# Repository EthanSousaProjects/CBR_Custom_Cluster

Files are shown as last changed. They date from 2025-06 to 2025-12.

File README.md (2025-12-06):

# CBR_Custom_Cluster

A custom cluster design for my CBR 125RW6 (2006 carburetor model) to replace the old large mechanical cluster with a smaller simpler design.

The `references` folder contains details on set things on the bike (eg. hole position dimensions, resistance of stock sensor) and thus design requirements, calculations and decisions can be found here.

## License

There are three licenses for this project. All code falls under the AGPLV3 license, all hardware designs fall under the CERN-OHL-S license, all artwork and documentation in the READMEs related to this project are under the CC By-SA license.

This project is based around creating a dash for a honda motorcycle. I have no affiliation with honda or its subsidiaries. This is not an official honda project in anyway.

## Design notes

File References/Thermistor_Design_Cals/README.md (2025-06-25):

# Thermistor Design Calculations

This document details set properties of the stock thermistor of the CBR 125RW6 radiator and the design decisions made because of it. It is supported by charts mathematical equations.

All charts are made in the file: `Design_Charts.ods` it is a Libre Office Calcs document.

## The Active resistance Range of the sensor

From the [Haynes cbr125r manual](https://haynes.com/en-gb/honda-motorcycle/cbr125r/2004-2010) wiring diagram it is clear that the sensor is a thermistor that is wired to ground and the dash sensor. The coolant temperature gauge has 3 wires connected to it: one for Voltage in, One for ground and one wire which goes to the sensor which is also wired to ground. I could not find resistance values of the sensor which match up with the needle positions of the gauge from the manual. Therefore, testing was required to find the resistance values the sensor can achieve and what that would look like on the gauge.

This testing was conducted by powering the gauge with 12 volts through the power pins (Vin and ground) determined from the wiring diagram in the manual. Then connected the sense wire to one end of a resistor/ resistor chain (resistors in parallel) with the other end of the resistor / resistor chain to ground. This simulates the thermistor at a specific resistance which would normally correspond to a certain temperature. The needle position will be noted and the resistance adjusted until we found resistances that matched up with needle positions of interest. Those positions being:

- Just letting off cold side limit

- 25% mark

- 50% mark

- 75% mark

- Just before reaching hot side limit

This relationship was then put into a table and charted to analysis the relationship.

| Needle Position  | Resistance (Ohms) |
| --- | --- |
| 0% **(Note 1)**  | 1000 |
| 25% | 727 |
| 50% | 579 |
| 75% | 470 |
| 100%**(Note 2)** | 377 |

**Note 1:** When the needle just starts to move off edge. Any value above this will not move needle.

**Note 2:** When needle just reaches top edge. Any value lower than this will stay at the top edge.

If we were to chart this data including the effect of higher and lower resistances at the limits we would get:

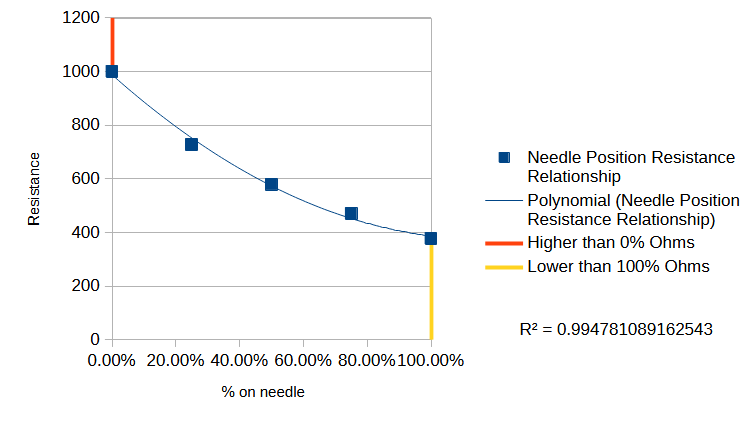
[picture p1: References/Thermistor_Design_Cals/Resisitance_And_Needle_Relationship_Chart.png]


From the results and charts gathered from the test we have determined the active range of the needle gauge on the stock bike and thus the range of interest for the new dash project.

## Nano Sensor Circuit Design

To detect the resistance value we need to use a [voltage divider](https://en.wikipedia.org/wiki/Voltage_divider) circuit. For our use case, our voltage divider circuit will look like:

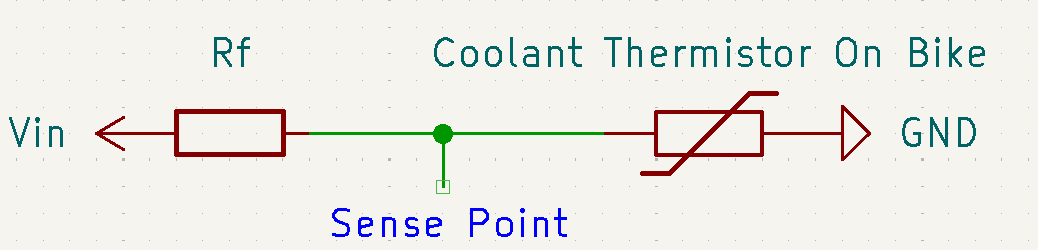
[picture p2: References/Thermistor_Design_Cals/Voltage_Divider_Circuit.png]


From this we can develop an equation to find the voltage at the sense point and as we know the voltage limit on the [Arduino Nano ESP32](https://docs.arduino.cc/hardware/nano-esp32/) is 3.3V set the voltage limit at the sense point.

$Vin { Rx \over Rx + Rf} \le 3.3V$

Where:

- $Rx$ is the resistance of the coolant thermistor on the bike

- $Rf$ is the fixed resistor we have to add

- $Vin$ is the source voltage into the line

If we think about what could happen in the circuit based on the data collected. It is possible in the most extreme cases for the sensor resistance to become practically 0 if the bike were to get too hot. Therefore, if we set $Rx$ to 0 Ohms and complete the calculation we find the $Vin$ must not exceed $3.3V$.

From this, we now know that $Vin$ must be $3.3V$ to get the largest sensing voltage range out of our micro controller.

It is also possible for the sensor to read infinite resistance if the bike were to get too cold. Therefore meaning that we can never reach a voltage sense of 0V as $Rx$ is the numerator of the fraction. We can however, find a $Rf$ value that will give us the most ideal voltage curve that is as linear as possible with a satisfactory voltage range.

To do this we can reconfigure our equation above to:

$3.3 {Rx \over Rx + Rf}=V_{sense}$

We can then use this equation to plot multiple lines of different $Rf$ values to find the most appropriate one.

If we first plot a chart of the voltage differences between the top and bottom values we get a chart like:

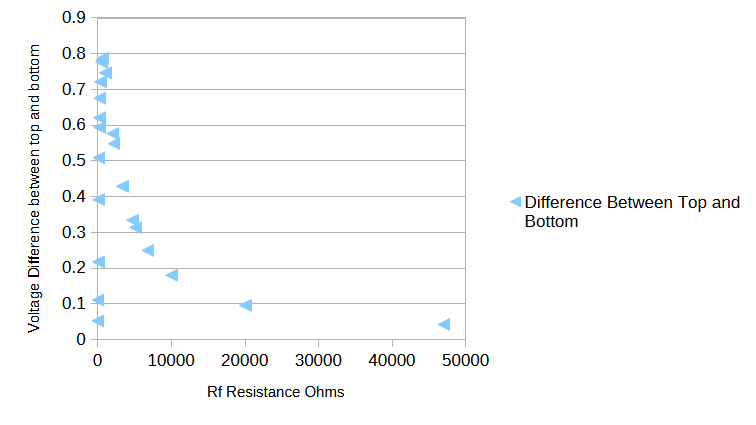
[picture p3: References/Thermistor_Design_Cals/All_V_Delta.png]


This cart shows us that in the best case scenario the voltage range is at best around 0.8V. This is very low but unfortunately we have a very large active range of the sensor so we have to use it. If we remove all the points with a Voltage delta of less than $0.5V$ we get:

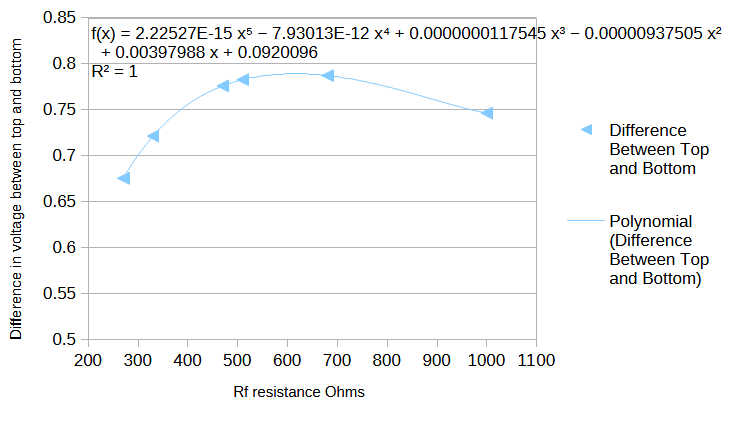
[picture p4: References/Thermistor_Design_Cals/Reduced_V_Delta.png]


We can plot a like onto this and see that we get a polynomial trend for the range of $Rf$ between approximately between 200 and 1100 Ohms.

We get a very good fit with a power of 5 polynomial (R value = 1). It also shows that the most ideal resistor is about 600 Ohms. As that is not a standard resistor I will choose either 510 or 680 Ohms. Either will be fine.

We may also want to have a look at the trend line between our points of interest of the reduced $Rf$ value range. We get a chart like the one bellow:

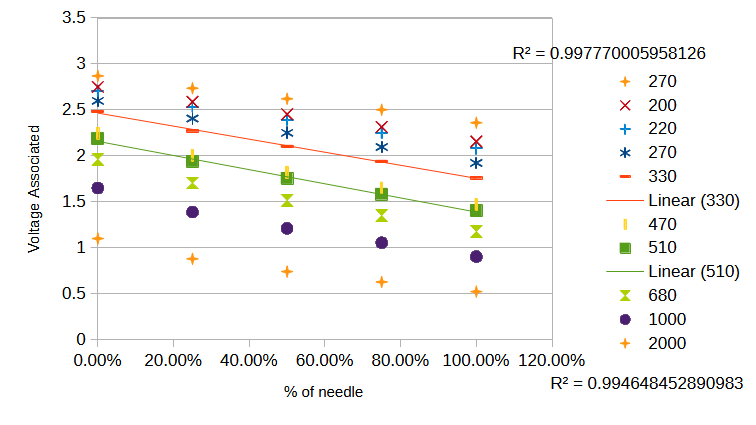
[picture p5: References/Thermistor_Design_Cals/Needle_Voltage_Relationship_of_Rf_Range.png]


We can see from this that between the points of interest we have a very linear relationship with high R values. Therefore, a linear relationship can be established and used in code making things simpler.

Due to the 12 bit resolution of the [Arduino nano esp32](https://docs.arduino.cc/tutorials/nano-esp32/cheat-sheet/) meaning we get values between 0 and 4095 (0V for 0, 3.3V for 4095) we can find the maximum amount of steps in our sensor. With a 510 Ohm resistor we get approximately a delta V of 0.77 volts.

Voltage per step: ${3.3 \over 4095} \approx 0.000806$

Amount of steps in interest range = ${0.77 \over 0.000806} \approx 955$ steps.

This range is satisfactory for my use case.

 From all this, a 510 Ohm resistor for $Rf$ will be used giving use satisfactory resolution.

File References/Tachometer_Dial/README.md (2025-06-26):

# Tachometer Dial Reference

This reference refers to the dimensions of the tachometer dial face which determines many of the PCB size and placement requirements and the mechanical design of the dash project.

The Tachometer face used is from a Honda CBR 600F as the max RPM value is similar to the CBR 125RW6 I have and I like how the dial is even on both sides of the center line instead of it being offset values. I also like it as the speedometer dial face is the same dimensions as the tachometer one allowing me to switch from a tachometer dial to a speedometer dial if I wanted to.

I purchased this dial gauge face from [newtacho.de](https://www.newtacho.de/shop/honda-en/speedometer-dials-gauge-honda-cbf-600/?lang=en) which is a German based company that sells around Europe but other sellers will likely offer the same thing.

The reference dimensions are found by taking a top down image of the dial face with a ruler next to it for scale. This is then imported into [FreeCAD](https://www.freecad.org/), scaled and draw over to get a CAD model of the dial face. Once a CAD model is made it is used to make an engineering drawing which is used as reference for a reference footprint in the Full circuit schematic. This CAD model is also used in the mechancial design as a reference for case dimensions.

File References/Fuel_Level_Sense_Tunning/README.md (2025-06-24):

# Fuel Level Reference Calculations conclusion

To use the stock fuel level sensor we have to understand how the current sensor operates in the bike.

From a [Haynes repair manual for the CBR 125R 2004-2010](https://haynes.com/en-gb/honda-motorcycle/cbr125r/2004-2010) manual for the CBR 125R. it states the following with regards for the resistance between wires of the fuel level sensor that go from the sensor up to the stock cluster:

| Wire Colors | Full Position | Empty Position |
| --- | --- | --- |
| Green - Blue/White | 556 Ohms | 33 Ohms |
| Green - Yellow/White | 33 Ohms | 556 Ohms |
| Blue/White - Yellow/White | 600 Ohms | 600 Ohms |

It must be noted that the Green wire is a ground wire on the bike. Therefore we can make the conclusion that the fuel sensor is a potentiometer where the ground is the whipper position. An image of the circuit can be seen bellow.

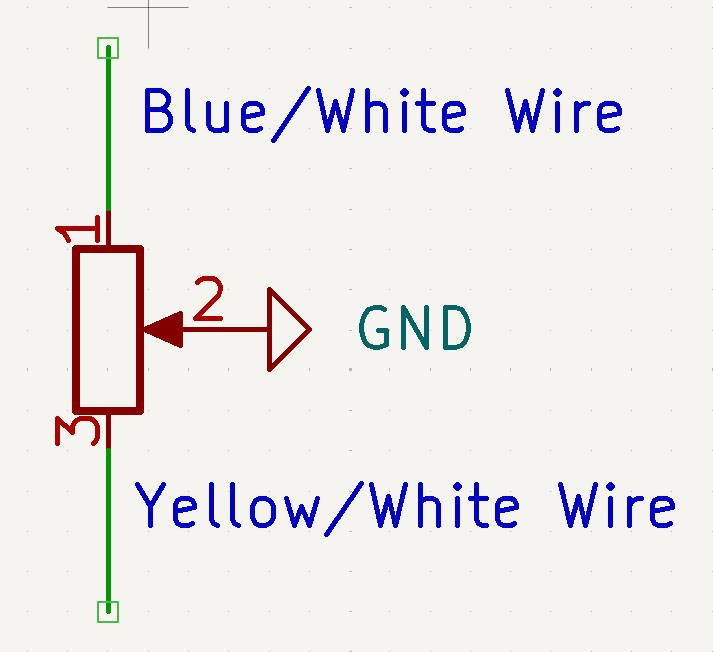
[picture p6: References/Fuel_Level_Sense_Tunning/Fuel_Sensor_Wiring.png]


Now that we know how the sensor is wired, we can create a circuit of how our system needs to be wiring together to measure the resistance of the sensor and thus determine how full the tank is. This will involve a [voltage divider circuit](https://en.wikipedia.org/wiki/Voltage_divider) to get a voltage between a known resistance and a variable one (the variable one being the sensor in this case).

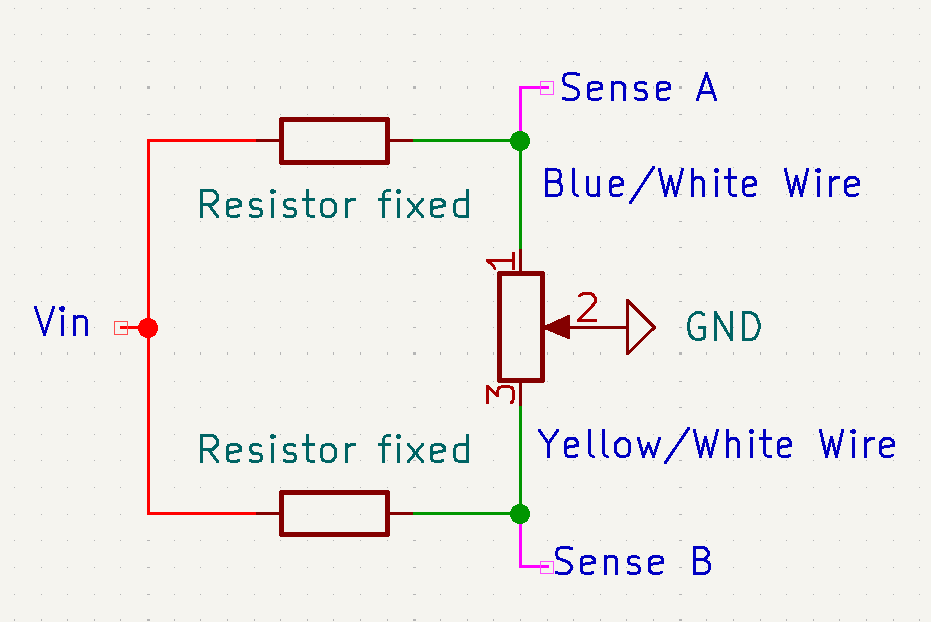
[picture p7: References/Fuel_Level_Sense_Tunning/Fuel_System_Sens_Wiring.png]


Now that we have developed the system wiring, we can develop equations to find the voltage at positions Sense A and Sense B. Please note that these positions will have identical reactions but in opposite directions. Thus we can find the fixed resistance in one leg and thus will know what is required for the other leg. Just note that resistance values correspond to opposite values of fullness.

$Vin{ {Rx} \over {Rt} } \le 3.3$ where $Rt = Rx + Rf$.

- $Vin$ is the driving voltage of the circuit. For my use case i will be using 9V as that is one of my standard voltages of my design.

- $Rx$ is the value of the potentiometer resistance. The values we are mostly interested in are the maximum and minimums which are 566 Ohms and 33 Ohms respectively. This is the driver for what the voltage will be at the sense side.

- $Rt$ is total resistance between the fixed resistor ($Rf$).

- The $3.3$ is the maximum voltage that my micro controller can take which is why it is on the right side of the inequality as for any $Rx$ value i need it to always be bellow $3.3 V$.

If we think about the [Equations behind a voltage divider](https://en.wikipedia.org/wiki/Voltage_divider) we will know that in our case the higher the $Rx$ value the higher the voltage will be. Therefore, we can find the minimum value of $Rf$ required to make sure the sense voltage never exceeds $3.3V$.

$9 {556 \over 556 + Rf} \le 3.3$

${556 \over 556 + Rf} \le {3.3 \over 9}$

$556 \le 0.36667(556 + Rf)$

${556 \over 0.36667} \le 556 + Rf$

$1543.5 - 566 \le Rf$

$977.5 \le Rf$

Therefore, $Rf$ must be greater than $977.5$ Ohms. If we use a standard resistor, the closest value higher than this is a 1 Kilo ohm resistor. This that is what will be used.

All further calculations are included in the file named `Level_VS_Resistance_Test_calcs.ods` which is a Libre Office Calc document.

With all this information, If we assume the relationship is linear between the resistance and fullness of the tank, we can predict how full the tank will be. It must be noted however that the voltage will not be linear. Therefore we will get some offset from the predicted value of fulness if we assume that the voltage is linear between fullness as well. This can be seen in the chart bellow:

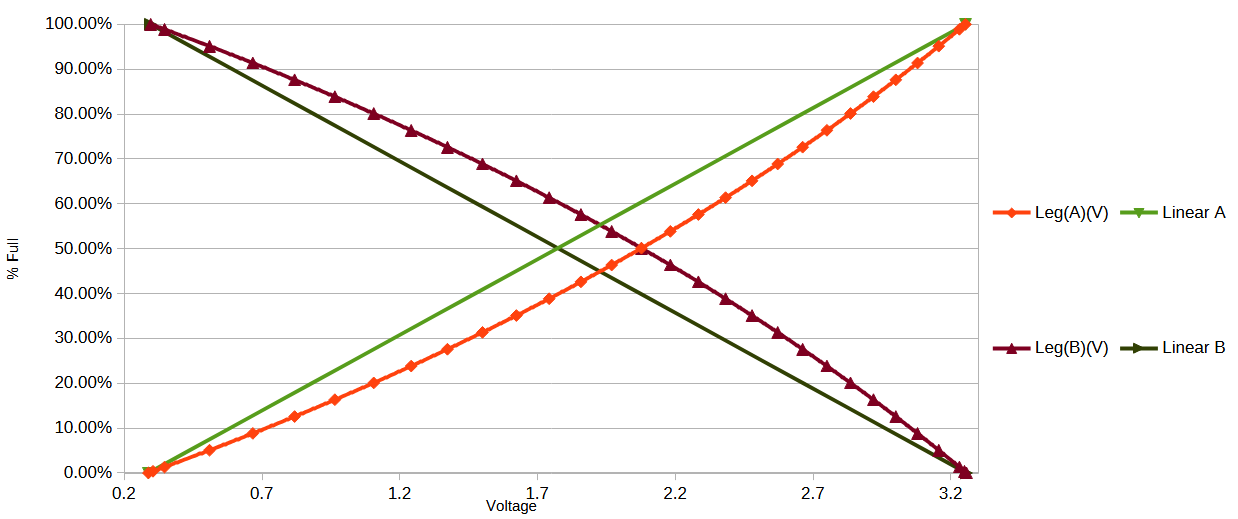
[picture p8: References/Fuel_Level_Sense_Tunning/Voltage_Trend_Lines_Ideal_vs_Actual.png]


To mitigate this we can use the average of the legs predicted values to get a value much closer to the actual value of the tank fullness. This can be seen in the chart bellow:

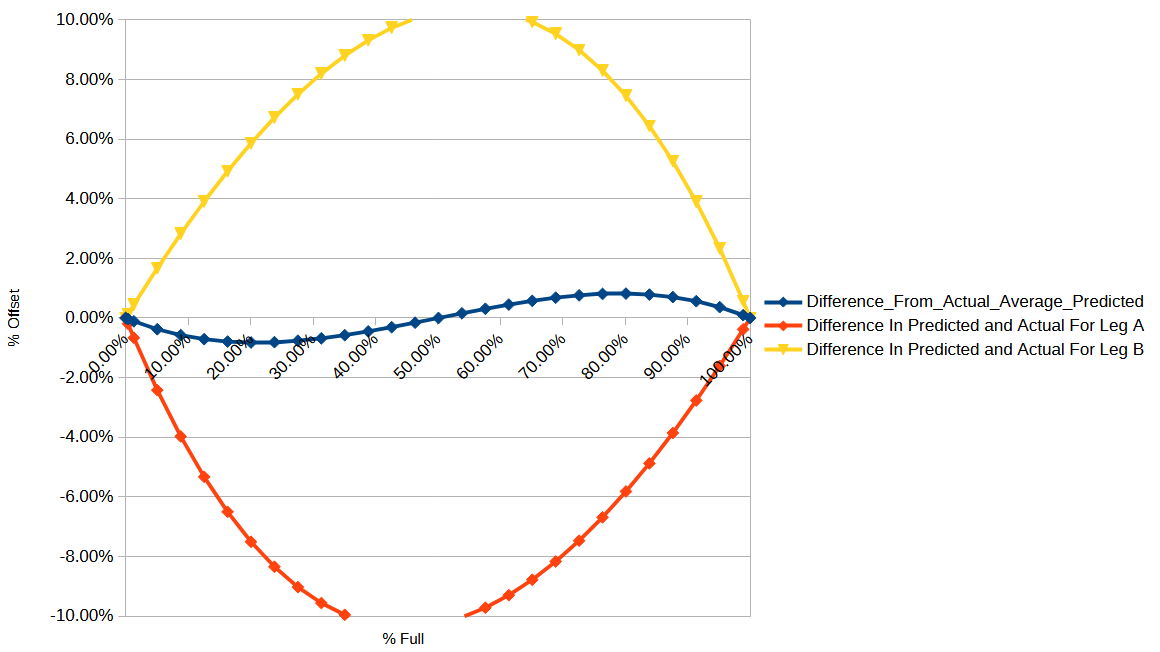
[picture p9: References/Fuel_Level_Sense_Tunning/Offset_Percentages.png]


We are not fully at the actual value but we are much closer compared to the upwards of 10% off if we were to only look at one leg. As very a precise accuracy is not needed the 1ish % offset is fine.

We now know the requires in our schematic for our dash and it can be implemented.

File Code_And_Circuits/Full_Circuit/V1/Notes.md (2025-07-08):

# Notes following the V1 design

- Through testing the following pin config is needed for the stepper to operate correctly `Stepper gauge_stepper(600, 2, 3, 5, 4);`

- Display works as expected using the testing code found in the test script folder. Makes a nice white colour with all the resistors.

- All power lines are working as expected getting all voltage levels i would expect

- Intesting note when powered on all lights sometimes pop on.

## Improvements for V2 design

- Make a smaller diameter.

- Consider a module based setup instead of using the nano for packaging reasons. (ESP32-S3 based) is more advanced and will need to worry about usb port but would help slim down packaging and may make more pins avaliable for usage.

- Consider the use of multiple PCBs

- Adjust capacitors to use standard values i have by putting them in parallel if needed as some values i do not have.

- Reconsider the power supplies, smaller?, Can i power nano with just 3.3V eliminatig need for 9V one, etc.

- Move all the components (caps, resistors, chips, etc) that do not have to be on the top layer to the bottom layer.

- Move all the traces to the bottom layer/ as many as possible.

- Try to implement the logging controller with GPS, SD card, etc

- Reconsider pinouts to work a bit better for the stepper driver to keep all pins on the same layer.

- Consider an SMD mounting for anything that is currently through hole. eg. steppper driver, nano, 

- Change 10 uF caps to electrolitic or decrease to be an SMD version (eg. 0.1 uF) 0.1uF for noise filtering and elecolitic to hold charge for componentes suddenly drawing it. Reconfigure it to work a bit better and ceramic caps do not reach high values.

- Add in underlights for RPM gauge/ speedo gauge that I forgot about. Make through hole 5mm ones or consider using standard W5W lights by putting holes in PCB at certain spots. Or consider using SMD mounting leds for smaller packaging.

- Reconsider mounting hole locations to be more evenly distrabuted.

- Reconsider some footprints that can be a socket instead of component directly soldered on.

- Implement diodes just maybe reconsider smd vs through hole

- re implement caps

- reconsider how display resistors are implemented as if want other colour than white really hard to desolder smd bits could make solder pad which could be good.

- Reconsider how to display speed can it work on the LCD as the alphanumeric takes up a bit too much space in current design. Testing required.

- Change the pins around after the logic level shifter to the stepper driver to keep all traces on the same layer and adjust pin config in code to suit.

## Extra notes on improvements and what to tackel.

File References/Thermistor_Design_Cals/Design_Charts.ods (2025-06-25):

 | Needle position and Resistance Relationship |  |  | Setup values
 | % on needle | Resistance (Ohms) |  | 1200 | 0
* | 0.00% | 1000
 | 25.00% | 727
 | 50.00% | 579
 | 75.00% | 470
** | 100.00% | 377
 | * Note 0 % on needle is when it just starts to move.
 | ** Note 100% on needle is when it just gets there.
 | Different Rf values test
 | Use standard Resistance values instead of custom so that standard resistor can be used Mainly testing with resistor range I personally have
 | % on needle | 0.00% | 25.00% | 50.00% | 75.00% | 100.00%
 | Resistance (Ohms) | 1000 | 727 | 579 | 470 | 377
 | Rf Values to test |  |  |  |  |  | Difference Between Top and Bottom
 | 10 | 3.26732673267327 | 3.25522388059701 | 3.24397283531409 | 3.23125 | 3.21472868217054 | 0.0525980505027248
 | 22 | 3.22896281800391 | 3.20307076101469 | 3.17920133111481 | 3.15243902439024 | 3.11804511278196 | 0.110917705221959
 | 47 | 3.15186246418338 | 3.09961240310078 | 3.05223642172524 | 3 | 2.93419811320755 | 0.217664350975834
 | 100 | 3 | 2.90096735187424 | 2.8139911634757 | 2.72105263157895 | 2.60817610062893 | 0.391823899371069
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

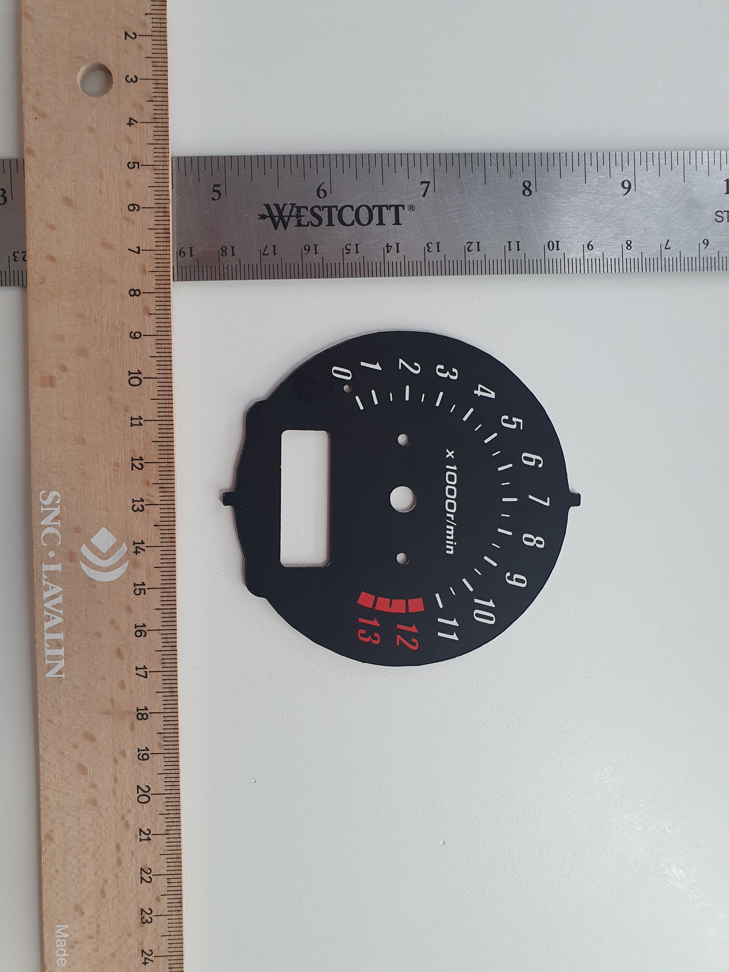
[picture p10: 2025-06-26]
References/Tachometer_Dial/Tach_Face_Reference_Image.jpg

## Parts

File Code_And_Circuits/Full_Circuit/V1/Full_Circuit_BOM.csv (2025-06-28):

Reference | Qty | Value | DNP | Exclude from BOM | Exclude from Board | Footprint | Datasheet
A1 | 1 | Arduino_Nano_ESP32 |  |  |  | Module:Arduino_Nano | https://docs.arduino.cc/resources/datasheets/ABX00083-datasheet.pdf
A3 | 1 | Arduino_Nano_ESP32 | DNP |  | Excluded from board | Module:Arduino_Nano | https://docs.arduino.cc/resources/datasheets/ABX00083-datasheet.pdf
C1,C5 | 2 | 1000PF |  |  |  | Capacitor_SMD:C_0805_2012Metric_Pad1.18x1.45mm_HandSolder | ~
C2,C3,C4 | 3 | 1000PF | DNP |  | Excluded from board | Capacitor_THT:C_Disc_D3.0mm_W2.0mm_P2.50mm | ~
C6,C19 | 2 | 0.1 uF |  |  |  | Capacitor_SMD:C_0805_2012Metric_Pad1.18x1.45mm_HandSolder | ~
C7 | 1 | 0.33uF |  |  |  | Capacitor_SMD:C_0805_2012Metric_Pad1.18x1.45mm_HandSolder | ~
C8,C9,C10,C11,C12,C13,C14,C15 | 8 | 1uF |  |  |  | Capacitor_SMD:C_0805_2012Metric_Pad1.18x1.45mm_HandSolder | ~
C16 | 1 | 100uF | DNP |  | Excluded from board | Capacitor_SMD:C_0805_2012Metric_Pad1.18x1.45mm_HandSolder | ~
C17,C18 | 2 | 10 uF |  |  |  | Capacitor_THT:C_Disc_D3.0mm_W1.6mm_P2.50mm | ~
D1 | 1 | LED_Right_Indicator(Yellow_LTH5MM12VFR4700) |  |  |  | LED_THT:LED_D5.0mm | ~
D2 | 1 | LED_High_Beam(Blue_LTH5MM12VFR4600) |  |  |  | LED_THT:LED_D5.0mm | ~
D3 | 1 | LED_Neutral(Green_LTH5MM12VFR4500) |  |  |  | LED_THT:LED_D5.0mm | ~
D4 | 1 | LED_Left_Indicator(Yellow_LTH5MM12VFR4700) |  |  |  | LED_THT:LED_D5.0mm | ~
D5,D7,D8,D9,D10,D11,D12,D13 | 8 | LED_2.2V_20ma |  |  |  | LED_THT:LED_D5.0mm | ~
D6,D14 | 2 | 1N4007 | DNP |  | Excluded from board | Diode_THT:D_DO-41_SOD81_P10.16mm_Horizontal | http://www.vishay.com/docs/88503/1n4001.pdf
DS1 | 1 | NHD-C12832A1Z-FS_RGB_-FBW-3V |  |  |  | Added_Footprints:NHDC12832A1ZFSRGBFBW3V
H1,H2,H3 | 3 | MountingHole |  | Excluded from BOM |  | MountingHole:MountingHole_3.2mm_M3 | ~
H4 | 1 | MountingHole | DNP | Excluded from BOM | Excluded from board | MountingHole:MountingHole_3.2mm_M3 | ~
J1 | 1 | Micro_SD_Card_Slot | DNP |  | Excluded from board | Connector_Card:microSD_HC_Wuerth_693072010801 | https://www.we-online.com/components/products/datasheet/693072010801.pdf
J2 | 1 | Main_Power_In_JST-XH |  |  |  | Connector_JST:JST_XH_B2B-XH-A_1x02_P2.50mm_Vertical | ~
J3 | 1 | Warning_Lights_JST-XH |  |  |  | Connector_JST:JST_XH_B4B-XH-A_1x04_P2.50mm_Vertical | ~
J4 | 1 | Signals_RPM_Temp_Fuel_JST-XH |  |  |  | Connector_JST:JST_XH_B4B-XH-A_1x04_P2.50mm_Vertical | ~
J5 | 1 | Speed_Pulser_Setup_Signal_JST-XH |  |  |  | Connector_Wire:SolderWirePad_1x01_SMD_1x2mm | ~
J6 | 1 | Alphanumeric_Qwiick_JST-XH |  |  |  | Connector_JST:JST_XH_B4B-XH-A_1x04_P2.50mm_Vertical | ~
JP1 | 1 | Pull up Jumper |  | Excluded from BOM |  | Jumper:SolderJumper-3_P1.3mm_Open_RoundedPad1.0x1.5mm_NumberLabels | ~
JP2 | 1 | address jumper A2 | DNP | Excluded from BOM | Excluded from board | Jumper:SolderJumper-3_P1.3mm_Bridged12_RoundedPad1.0x1.5mm_NumberLabels | ~
JP3 | 1 | address jumper A1 | DNP | Excluded from BOM | Excluded from board | Jumper:SolderJumper-3_P1.3mm_Bridged12_RoundedPad1.0x1.5mm_NumberLabels | ~
JP4 | 1 | address jumper A0 | DNP | Excluded from BOM | Excluded from board | Jumper:SolderJumper-3_P1.3mm_Bridged12_RoundedPad1.0x1.5mm_NumberLabels | ~
JP5 | 1 | Write Protection Jumper | DNP | Excluded from BOM | Excluded from board | Jumper:SolderJumper-2_P1.3mm_Open_RoundedPad1.0x1.5mm | ~
M1 | 1 | GY-GPS6MV2 | DNP |  | Excluded from board | Added_Footprints:GY-GPS6MV2
M2 | 1 | Stepper_Motor_bipolar |  |  |  | Added_Footprints:X27-168 | http://www.infineon.com/dgdl/Application-Note-TLE8110EE_driving_UniPolarStepperMotor_V1.1.pdf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
M3 | 1 | Accelerometer and Gyroscope (BMI160 Module) | DNP |  | Excluded from board | Added_Footprints:BMI160_Module
N1 | 1 | Tachometer Reference |  |  |  | Added_Footprints:Dial_Gauge_Reference_CBF600 | ~
R1,R2,R3,R4 | 4 | 200R |  |  |  | Resistor_SMD:R_0805_2012Metric_Pad1.20x1.40mm_HandSolder | ~
R5,R10 | 2 | 3.3KR |  |  |  | Resistor_SMD:R_0805_2012Metric_Pad1.20x1.40mm_HandSolder | ~
R6,R7,R8,R11 | 4 | 1KR |  |  |  | Resistor_SMD:R_0805_2012Metric_Pad1.20x1.40mm_HandSolder | ~
R9 | 1 | 510R |  |  |  | Resistor_SMD:R_0805_2012Metric_Pad1.20x1.40mm_HandSolder | ~
R12,R13,R14,R15,R16,R17,R18,R19 | 8 | 100R |  |  |  | Resistor_SMD:R_0805_2012Metric_Pad1.20x1.40mm_HandSolder | ~
R20 | 1 | 10KR |  |  |  | Resistor_THT:R_Axial_DIN0204_L3.6mm_D1.6mm_P7.62mm_Horizontal | ~
R22 | 1 | 56R |  |  |  | Resistor_SMD:R_0805_2012Metric_Pad1.20x1.40mm_HandSolder | ~
R23,R24 | 2 | 6.8R |  |  |  | Resistor_SMD:R_0805_2012Metric_Pad1.20x1.40mm_HandSolder | ~
R25,R26 | 2 | 4.7KR |  |  |  | Resistor_SMD:R_0805_2012Metric_Pad1.20x1.40mm_HandSolder | ~
R27,R28,R29,R30 | 4 | 100KR | DNP |  | Excluded from board | Resistor_SMD:R_0805_2012Metric_Pad1.20x1.40mm_HandSolder | ~
SW1 | 1 | SW_Push_JST-XH_Input |  |  |  | Connector_JST:JST_XH_B2B-XH-A_1x02_P2.50mm_Vertical | ~
TP1,TP2,TP3 | 3 | TestPoint |  |  |  | Connector_PinHeader_2.54mm:PinHeader_1x01_P2.54mm_Vertical | ~
TP4,TP5,TP6 | 3 | TestPoint | DNP |  | Excluded from board | Connector_PinHeader_1.00mm:PinHeader_1x01_P1.00mm_Vertical | ~
U1 | 1 | R-78E3.3-0.5 |  |  |  | Converter_DCDC:Converter_DCDC_RECOM_R-78E-0.5_THT | https://www.recom-power.com/pdf/Innoline/R-78Exx-0.5.pdf
U2 | 1 | L293D |  |  |  | Package_DIP:DIP-16_W7.62mm | http://www.ti.com/lit/ds/symlink/l293.pdf
U3 | 1 | TEC2-1219WI |  |  |  | Converter_DCDC:Converter_DCDC_TRACO_TMR-xxxx_THT | https://www.tracopower.com/products/tec2wi.pdf
U4 | 1 | L7805 |  |  |  | Package_TO_SOT_THT:TO-220-3_Horizontal_TabDown | http://www.st.com/content/ccc/resource/technical/document/datasheet/41/4f/b3/b0/12/d4/47/88/CD00000444.pdf/files/CD00000444.pdf/jcr:content/translations/en.CD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
U5 | 1 | TXB0104D |  |  |  | Package_SO:SOIC-14_3.9x8.7mm_P1.27mm | http://www.ti.com/lit/ds/symlink/txb0104.pdf
U6 | 1 | 74HC595 |  |  |  | Package_DIP:DIP-16_W7.62mm_Socket | http://www.ti.com/lit/ds/symlink/sn74hc595.pdf
U7 | 1 | CAT24C128 |  |  |  | Package_SO:SOIC-8_3.9x4.9mm_P1.27mm | https://www.onsemi.com/pub/Collateral/CAT24C128-D.PDF

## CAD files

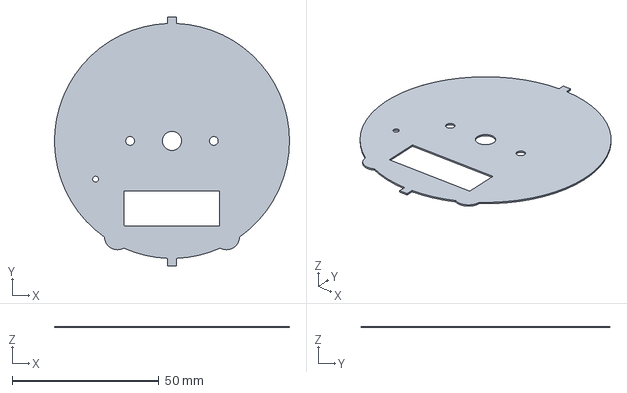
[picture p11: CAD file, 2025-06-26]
References/Tachometer_Dial/Tach_Face_Reference_CAD_Model.FCStd
80.0 x 84.7 x 0.5 mm

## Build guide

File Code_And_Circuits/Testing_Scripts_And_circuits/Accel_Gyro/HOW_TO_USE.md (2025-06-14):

# Accelerometer and Gyroscope module data collection.

This testing script and circuit is used to test the functionlity of the BMI160 6 axis accelerometer and gyroscope. Specifically the I2C interface (there is an SPI interface I am not using). This script is based around using an arduino Nano running the script but, any board with I2C compatability should work. You will just have to change the ini file if you do.

For the BMI160 i purchased it from [Kunkune](https://kunkune.co.uk/shop/arduino-sensors/bmi160-6-axis-motion-tracking-accelerometer-gyroscope-module/) but there are other retailers selling the same module.

There is a schematic and test PCB made in KICAD in the folder `Circuit_Accel_Gyro` of how  everything should be connected together when using the I2C interface.



Once everything is connected make sure the [DFRobot BMI160](https://docs.arduino.cc/libraries/dfrobot_bmi160/) library is installed and avaliable to the project. Compile and upload the code. When you connect the board to the serial terminal you should see the acceleration and gyroscope values appear. These are the raw values from the sensor every secound just so that you are able to read the values a bit easier to read. To get more accurate values for processing you will need to remove the delay of 1000ms to increase your sampling rate.

I have not done any post processing on this script to get things like pitch and roll but i have come accross a few resources on the mathematics behind it if you are interested.

- [ESP32 with BMI160 Accelerometer & Gyroscope Sensor](https://how2electronics.com/esp32-with-bmi160-accelerometer-gyroscope-sensor/)
- [Measure Pitch, Roll, Yaw with MPU6050 + HMC5883L & ESP32](https://how2electronics.com/measure-pitch-roll-yaw-with-mpu6050-hmc5883l-esp32/)
- [Measuring Roll, Pitch, and Yaw Using 3-Axis Gyro on the MPU6050](https://toptechboy.com/measuring-roll-pitch-and-yaw-using-3-axis-gyro-on-the-mpu6050/)
- [Towards understanding IMU: Basics of Accelerometer and Gyroscope Sensors and How to Compute Pitch, Roll and Yaw Angles](https://atadiat.com/en/e-towards-understanding-imu-basics-of-accelerometer-and-gyroscope-sensors/)
- 

Big thanks to the DF robot team on their library and [their tutorial on their module](https://wiki.dfrobot.com/Gravity__BMI160_6-Axis_Inertial_Motion_Sensor_SKU__SEN0250) which was helpful for me getting my module to work.

Big thanks to [hanyazou](https://github.com/hanyazou) on github for his [BMI160 library README.md](https://github.com/hanyazou/BMI160-Arduino) helping me to wire my sensor together.

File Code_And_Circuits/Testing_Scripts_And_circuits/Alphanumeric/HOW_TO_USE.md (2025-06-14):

# Testing the Spark fun alpha Numeric Display

This testing sript and circuit is used to test the functionality of the SparkFun Qwiic Alphanumeric Display in it's ability to display letters and numbers (speed and units kph or mph). This is based around using an Arduino nano running the script but any board with I2C and the [SparkFun Qwiic Alphanumeric Display Arduino Library](https://docs.arduino.cc/libraries/sparkfun-qwiic-alphanumeric-display-arduino-library/) compatability should work. You will just have to change the ini file if you do.

For this display i purchased it from [Pihut](https://thepihut.com/products/sparkfun-qwiic-alphanumeric-display-purple). I specifically purchased the purple one due to my bikes purple theme. There are other colours. Other colours are avaliable like red, green, blue, white, etc. to fit your wants. You will need to get a qwiic breakout if you do not have a qwiic plug on your device like me. You could also solder header pins to the board following the [hookup guide from sparkfun](https://learn.sparkfun.com/tutorials/sparkfun-qwiic-alphanumeric-display-hookup-guide/all) but i would recommend getting the adaptor cable.

There is a schematic and test PCB made in KICAD in the folder `Circuit_Alphanumeric` of how everything should be connected together. You will require a breakout cable in my design.



Once everything is connected make sure the [SparkFun Qwiic Alphanumeric Display Arduino Library](https://docs.arduino.cc/libraries/sparkfun-qwiic-alphanumeric-display-arduino-library/) is installed and avaliable to the project. Compile and upload the code. You should see all the segments light up. Then you should see a small k is added to the last digit and the display counts up by 1 to 100. Finally, it repeats the counting to 100 but changes the last digit to a small m.

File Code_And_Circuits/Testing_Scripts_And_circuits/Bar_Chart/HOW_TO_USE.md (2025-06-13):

# Bar chart controlled by arduino with shift registers

This testing script and circuit is to the test the functionallity running a LED bar chart off an arduino using a 74HC595 shift register. This allows us to use more LEDs while not taking up too many of our arduino pins. This script is based around an arduino nano but any micro controller should work if you change the board in platform IO.

The 74HC595 shift register gives us the ability to drive 8 LEDs while only using 3 digital pins. This allows us to drive more LEDs than the arduino may normally be able to. I have two which i have purchased from [Kunkune](https://kunkune.co.uk/shop/compatible-with-arduino-compatible-starter-kits/advanced-arduino-r3-compatible-starter-kit/) as part of an arduino kit and [Pihut](https://thepihut.com/products/74hc595-shift-register-3-pack). There are methods to drive multiple of these shift registers in series in eachother. See [this arduino tutorial from Carlyn Maw & Tom Igoe](https://docs.arduino.cc/tutorials/communication/guide-to-shift-out/).

There is a scematic and test PCB made in KICAD in the folder `Circuit_Bar` of how everything should be connected together. You can change around the digital pins just remember to change it in the script as well.



Once everything is connected, compile and upload the code. You should slowly see all the lights light up in sequence before resetting. Some of the sequence is faster than other points due to how the incrementing loop works.

Some complexity of the code you may not understand imeditatly is the [byte](https://docs.arduino.cc/language-reference/en/variables/data-types/byte/) data type and the `<<` operation. The `<<` is a [bit shift left operation](https://docs.arduino.cc/language-reference/en/structure/bitwise-operators/bitshiftLeft/) to help me get the bits in the bytes setup correctly to light up the 0 to x lights. I am basically getting an integer from that operation subrating 1 and then converting back to a byte. [Conversion from Binary to decimal explaination can be found here](https://www.tutorialspoint.com/how-to-convert-binary-to-decimal).

Big thanks to [Elego](https://www.elegoo.com) for their [Arduino tutorials](https://www.elegoo.com/en-gb/pages/download) which got me started with this.

Big thanks to [Jason Clark](https://arduino.stackexchange.com/users/28183/jason-clark) on arduino Stack Exchange for his help on getting a [better way to calculate 2^X instead of using the arduino `pow()` function](https://arduino.stackexchange.com/questions/31191/is-there-a-non-float-alternative-to-pow).

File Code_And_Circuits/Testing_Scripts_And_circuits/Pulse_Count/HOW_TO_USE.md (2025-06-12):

# Pulse Counter for Speed and RPM measurments

This testing script and circuit is used to test a pulse reading/ measuring script. This can then be used to translate the electrical pulses from the speed sensor and/or RPM pulses into speed or RPM data to be displayed on the dash. It is based on using an arduino nano running the RPM_TO_PWM script that is part of the `Testing_Scripts_And_Circuits` folder of this project and using a DOIT ESP32 devkit V1 to figure out the rpm/ count the pulses coming from the nano. Both scripts should work on any other microcontroller using the arduino framework.

It can be noted that we can find the rpm value by finding the time period of a pulse. We can then convert that to a frequency of pulses (... Hz). Once we have the frequency multiplying it by 60 would five the RPM value if you get one pulse per revolution. Slight math adjustment would be needed if you get something different to 1 pulse per rotation.
Speed is a tad more complicated but we can use the same theory of measuring the time of a pulse. If using something like a set of magnets, equally spaced on a wheel with a hall effect sensor picking them up. The time period would be the angle traveled between the two magnets. If we know the diameter or circumfrance, we could find the distance traveled along the circumfrance of the wheel. Therefore we would have distance and time and thus, speed = distance/ time.

It is important to note that the arduino works on 5V and the DOIT esp32 works on 3.3 volts thus a voltage divider was required for my use case. If alternative boards are used please make sure the voltage pulse measured is close to/ is the working voltage of micro controllers. Sending a 5V pulse to a 3.3V device may break the 3.3V device and sending a 3.3V pulse to a 5V device may just not recognise the signal as high.

There is a scematic and test PCB made in KICAD in the folder `Circuit_GPS` of how everything should be connected together. If you are not using the same boards as me, please adjust the voltage divider (resistors) to something more appropriate. Please also connect the grounds of the micro controllers together so that there is a common ground reference point/ plane.

Please note that the Kicad scematic uses a arduino nano ESP32 board instead of the DOit board. The connections are very similar just make sure the pin definitions are correct. I was unable to find a footprint for the DOIT dev kit. The important bit is the circuit divider taking the 5V pulse down to 3.3V if it is required. If it is not then you do not need to have it.



Once everything is connected, start both boards up having a serial monitor attached to each. On the nano you will have to type a RPM value to start the pulsing and on the measurment side you should see RPM and speed values. Verify they are as you expect by making some hand calculations based on your input parameters.

Big thanks to [TinkeringEngineer](https://www.instructables.com/member/TinkeringEngineer/) on instructables with his [Use Arduino to Display Engine RPM project](https://www.instructables.com/Use-Arduino-to-Display-Engine-RPM/) which helped me here improve on my initial idea for calculated speed and rpm.

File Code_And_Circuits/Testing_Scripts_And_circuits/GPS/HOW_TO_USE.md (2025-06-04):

# Recieving GPS data test for CBR dash project

This testing script and circuit is to the test the functionallity of recieving GPS based data to eventually  be used in the dash project for ride logging where i could track a ride. Originally i thought i would use it for a speed value but due to reliabilty issues i have decieded against it. The Script is based around an arduino nano but any micro controller should work if you change the board in platform IO.

Most GPS modules you can buy online work pretty much the same and the most important pins are the power in (VCC/ VIN and GND) and the RX and TX pins. Most other pins are only there for advanced/ more complicated uses. Therefore, all my diagrams / discussions will only discuss those 4 pins. I have purchased a NEO-6M GPS module from [Kunkune](https://kunkune.co.uk/shop/communication-boards/gy-neo6mv2-gps-module-super-signal-with-antenna/). If you are to get a different GPS module, everything here should work. I would recommend getting a module with an external antenna to help with signal reliability. This module has a baud rate of 9600 so will use that for my serial interface. If you have a different baud rate of your module use that specified baud rate.

There is a scematic and test PCB made in KICAD in the folder `Circuit_GPS` of how everything should be connected together. Please note that the rx and tx lines connect to digital pins so that we can use the [software serial](https://docs.arduino.cc/learn/built-in-libraries/software-serial/) library as if we used the built in rx and tx lines we would loss USB serial communication to see things on the board. Please also note that the rx pin lines up with the software tx pin and vis versa for the tx pin. Reversing this will orientation will make the module not work.



Once everything is connected, make sure that the [TinyGPSPlus](https://docs.arduino.cc/libraries/tinygpsplus/) external libarary is installed for the project to parse the [GPS NEMA string](https://aprs.gids.nl/nmea/#vtg). compile and upload the code. If the USB serial interface you should see the current satalites attached, the longitude and latitiude and the speed of the module. If you are inside you may struggle to connect to any satalites thus being outside in an open area in prefered. Once you get a fix the values should all change to a different value than 0.

Big thanks to the developers behind the [software serial](https://docs.arduino.cc/learn/built-in-libraries/software-serial/) library for arduino and the [TinyGPSPlus](https://docs.arduino.cc/libraries/tinygpsplus/) library.

Big thanks to [random nerd tutorials](https://randomnerdtutorials.com/) for there article on the [NEO-6M GPS Module](https://randomnerdtutorials.com/guide-to-neo-6m-gps-module-with-arduino/) helping me with the coding of the module.

Big thanks to [last minute engineers](https://lastminuteengineers.com/) for there in depth article on the [NEO-6M GPS Module](https://lastminuteengineers.com/neo6m-gps-arduino-tutorial/) where i learned alot about the specifics of the module itself.

Lastly big thanks to the [Core electronics youtube creator](https://www.youtube.com/@Core-Electronics) and there video on [adding GPS to a raspberry pi pico](https://www.youtube.com/watch?v=CLsXnSOIYMg) where i learned alot about the inner workings of GPS.

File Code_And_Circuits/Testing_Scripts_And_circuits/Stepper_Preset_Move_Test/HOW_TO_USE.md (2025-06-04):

# Stepper Preset Move Test for CBR Dash Project

This testing script is used to test the wiring and usability of the X27.168 automotive gauge stepper motor with a L293D dual H bridge motor driver. The script attempts to move the stepper a set distance clockwise/ anticlockwise, then the same distance in the oposite rotation. Then half way in the original direction. Then make a half rotation in the oposite direction again.

The stepper motor is from [adafruit](https://www.adafruit.com/product/2424#technical-details) but i purchased the stepper from a reseller in the UK called [pihut](https://thepihut.com/products/automotive-gauge-stepper-motor). The L293D is fairly generic and can be found on most electronics sellers. I purchased this [driver from pihut](https://thepihut.com/products/dual-h-bridge-motor-driver-for-dc-or-steppers-600ma-l293d).

According to the [technical details](https://www.adafruit.com/product/2424#technical-details) provided by adafruit this stepper motor has a maximum step count of 600 steps which is approximatly 315 degrees so each step is approximatly half a degree. Therefore, to test the stepper system, the script will move 600 steps, then -600, then 300 then -300.
During this movement, you should see the needle rotate approximatly 315 degrees, then -315 degrees, 157 degrees then finally -157 degrees. This will help determin if the circuit is setup correctly and if the rpm set is at an appropriate value.

A wiring scematic and testing PCB has been included in the `Circuit_Stepper` folder for your reference. You can change which pins are used as mine was based on how I had everything layed out on a breadboard.



Once everything is connected, make sure the external stepper library has been added to the platformIO project, compile, upload and run the script. If everything is connected correctly, you should see the stepper move. You may have to adjust your stepper speed to make sure it does not skip. After testing i found 20 rpm to be the maximum thus will run mine at 19 rpm.

Thank you to [Joshua Hrisko](https://makersportal.com/blog?author=59b036fc6073554c1cfffef7) for his [write up](https://makersportal.com/blog/2018/1/29/driving-any-stepper-motor-for-less-than-1-with-the-l293) on how to do this and the developers behind the [arduino stepper library](https://docs.arduino.cc/libraries/stepper/#Usage/Examples).

Big thanks to [Wiktor Burdecki](https://github.com/wiciu15) and his github project named [motoHUDsch](https://github.com/wiciu15/motoHUDsch/tree/master) where he made a [KICAD footprint of the 27.168 stepper motor](https://github.com/wiciu15/motoHUDsch/blob/master/motoHUD.pretty/X27-168.kicad_mod) which i have taken as a base to build off and slightly modified it to fit the datasheet for the stepper motor i found [here](https://4tronix.co.uk/zeropoint/x27_spec.pdf) and the one [adafruit](https://cdn-shop.adafruit.com/product-files/2424/2424.pdf) provided.

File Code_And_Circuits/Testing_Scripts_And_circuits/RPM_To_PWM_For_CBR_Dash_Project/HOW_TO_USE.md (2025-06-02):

# RPM to PWM For CBR Dash Project

This testing script is used to produce a signal matching that of the RPM pulse that comes from the CBR when it is turned on. It is designed to run on an arduino nano but by changing the board target, the script should work on other boards.

Made in VS code Platform IO extension (see main README.md for usage information).

The signal gets outputted on pin 13 (D13)(Make sure to connect grounds). A schematic and kicad PCB can be found in the folder `Circuit_RPM_TO_PWM`.

To get this to work, compile and upload code to the nano/ board and connect a serial monitor as the signal does not start without it. The serial monitor tells you how to select an RPM value and when the signal is running and at what simulated RPM is. Use a keyboard only typing in numbers where relevenent and only charters when relevent.

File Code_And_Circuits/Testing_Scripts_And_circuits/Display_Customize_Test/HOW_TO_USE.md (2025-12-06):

# Customizing display testing for CBR dash project

This testing script has been created to test the functionality of using the [U8g2 graphics library for monochrome displays](https://github.com/olikraus/u8g2) on the [NHD-C12832A1Z-FS(RGB)-FBW-3V](https://newhavendisplay.com/128x32-graphic-cog-lcd-fstn-display-with-rgb-backlight/) Newhaven display that will be used for the dash.

This script will include rendering of speed, trip and odometer data. This will cycle through a few numbers to see what it looks like. It will also cycle through different layouts and fonts to see all of them to choose the best one for the dash.

The circuit is the V1 version of the PCB. You could directly wire it instead of using the PCB but for testing to make sure the PCB was correct i used this.

An important note is that I am using the hardware SPI to run my display. That will effect the setup code. The controller on this display is the ST7565R SPI controller this also has an effect on the code if you are using something different. See code comments for better info on setting up the display correctly.

## Unique non ideal wiring and Pin Assignment

An important note on my setup is that I have used one of the hardware SPI pins as the dc pin also known as the A0 pin or register select pin in my use case. I have specifically used the Controller In Peripheral Out (CIPO) (also known as the Master In Slave Out (MISO)) pin as the dc /register select/ A0 pin. This causes some issues as the pin does not get correctly setup when initializing the display class using hardware SPI. To fix this I added in the following code before and after the `u8g2.begin();` line to fix it:

```c++
  pinMode(12,OUTPUT);
  digitalWrite(12,LOW);
```

Ideally you would avoid using any of the hardware SPI pins that are not necessary. However for my use case I was running out of available pins to utilize for the dash so used it.

## Custom Graphics (GIMP method)

I have made some custom graphics that I have used in the testing scripts. This was so that I could load them onto the display to see what it would look like. Some of these graphics will also be used on the final design.

To create all the graphics I used [gimp](https://www.gimp.org/) the file of which is saved in the `Custom_Images` folder.

To setup gimp for this display follow the guide bellow. Note that adjustments can be mode if using a different sized display in the appropriate places (eg 128 by 64 instead of 128 by 32):

1. Create a new file through `File > New`. Setting the image size to your specific display in Pixels(px). For my display it is 128 width, 32 height.

2. For new files the default colour setting is RGB. to set the black and white setting of the lcd graphics display enter `Image > Mode > Indexed`. In this menu select the `Use black and white (1-bit pallet)`. This will set your workspace to be only black and white.

3. If your grid has not appeared. It could be beneficial to you to see it by ticking the toggle in `View` called `Show grid`.

4. Use the pencil tool with the colour set to black and the size set to 1 to start making graphics.

5. Now you are able to draw any graphic you like. To allow for multiple graphics i used layers instead of creating many different files. When exporting I just selected the layers I wanted to see when exported. To add a layer go into `Layer > New Layer...`. In the menu make sure to set the layer to transparent. Now just make the relevant layers visible when you want to export the images.

6. You can import images into gimp to convert them to the bitmap type by dragging the image file into gimp. This can allow you to use images that have been created already which contain more detail but contain the overall shape you want to create in a graphic lcd form. I am not responsible for any copy write or trade mark infringement that may come from you doing this. Any images uploaded to this repo have been made by myself.

    - You may have to resize the image to fit on the display. To do this, select the layer the image is on and go into `layer > Scale layer...`. In the menu select the interpolation method of your choosing (I typically just use none but you can experiment with the different types) adn adjust the image pixel size that works for your use case.
    - Sometimes you may also have to reset the colour mode as importing images may add greyscale elements. The best way to handle this is to set the mode to greyscale or colour instead of indexed then index it again like in step 2. I have found that this normally fixes my issues.

7. Now that the images have been created. We are ready to export it to a C++ file we can load into the arduino nano esp32.

    - Activate the layers you want to export.
    - To export correctly go into `file > Export AS...`
    - In the menu that appears choose the file type of `X BitMap Image` with the file extension of xmb.
    - Make sure to uncheck the X10 format bitmap option if it is checked.
    - Make sure you remember what folder you export to.
    - The image is now exported correctly.

8. In the bitmap image file created in step 7 we can open the file in any text editor/ IDE. In it you will see some define terms at the top of your display size described with a charter array like declaration bellow it starting with `static unsigned char` etc. This is what needs to be copied into our script to be loaded.

9. In the script use the `u8g2.drawXBM(<int y position start>,<int x position start>,<int Display width in pixels>,<int Display height in pixels>,high30seg);` class function to display it to the screen.

Something extra you can do is to load all the images into a header file like I have with this script to decrease the clutter in the main script file. Just make sure you import the header file with the command `#import "<file name>.h"` the the start of the main script.

## What was learnt/ Liked

Through the use of this test script on the display the following conclusions on the different graphics have been made.

- Overall the display was readable in the dash and it would not be necessary to get a larger display for the dash. However, if you struggle to see I would recommend getting a larger dash like the [NHD-C12864DA-FSRGB-FBW-3V3](https://newhavendisplay.com/128x64-graphic-cog-lcd-fstn-wide-view-with-rgb-backlight-and-pins/) from [NewHaven Displays](https://newhavendisplay.com/) for readability reasons. It can be slightly difficult at times to read the display perfectly.
- If you are overlaying multiple bitmap images over each other, you must set the bitmap mode to 1 (transparent = true). This is done via the `.setBitmapMode(<1 for transparent, 0 for opaque>);` function of the display object more information can be found on the [u8g2 coding reference wiki page](https://github.com/olikraus/u8g2/wiki/u8g2reference#setbitmapmode).
- Making and loading bitmap images worked very well. Using them to make static non updating components like RPM, fuel and coolant graphics to then overlay data on top like speed is a good practice. I will use some of the graphics in my private library as a startup sequence graphic when the bike first turns on. I cannot upload them to github due to copyright unfortunately. I would recommend using this to help make static graphics.
- When testing the [Tom Thumb](https://robey.lag.net/2010/01/23/tiny-monospace-font.html) (u8g2_font_tom_thumb_4x6_mn) font, it was found to be too small and nearly unreadable even when resting on a desk. Therefore, reading it on a moving/vibrating motorcycle was going to be next to impossible. Although the font was very small it could still be used for things like odometer data when it needs to be squeezed onto the screen like the tachometer display as any other font was a bit too big. Ideally this font will not be used.
- An alternative to the tiny font that was much more readable while still being compact was the [u8g2_font_5x7_mr](https://github.com/olikraus/u8g2/wiki/fntgrpx11#5x7) font. This font will be the preferred one for any very small text and numbers like odometer and trip data.
- Through testing I found non bold fonts looked better for my use case in my opinion. The 30 high segment test shows this the best. I believe the non bold version of the font looks better in that test over the bold version of the font test. Therefore, non bold fonts will be used in the final dash.
- I think that the 30 pixel high digit segments worked ok but, by not utilizing the full height of the screen, it made it not work as well as the 32 pixel high  digit segment. I also really liked the appearance of the segment. Therefore, it will be used in the final solution in some way.
- I liked the [u8g2_font_t0_30_mr](https://github.com/olikraus/u8g2/wiki/fntgrpttyp0#t0_30) font for displaying the kph value so I will be using it in the final solution.
- I did not like the [u8g2_font_VCR_OSD_mr](https://github.com/olikraus/u8g2/wiki/fntgrpdafont#vcr_osd) font. It looked off to me for this use case. Therefore, it will not be used.
- The spacing of the kph lettering and Odometer data was perfect in the font based speed representation test for me. This spacing will be used to represent speed data on the final solution.
- In the font based speed representation test I liked the [u8g2_font_inr33_mn](https://github.com/olikraus/u8g2/wiki/fntgrpinconsolata#inr33) font to represent speed data. This font will be one of the solutions to display speed data in the final solution.
- For the RPM tests I liked the same RPM version (version a/1). The only disadvantage was the font size used for odometer data. This will be available in the final solution with a different odometer font being utilized. This version will be much simpler to code up as well compared to the ramping one as a bonus.
- Although Coolant and Fuel data is supposed to be represented by the lights on the dash, I liked the ramping coolant and fuel bars representation. The large gap in the middle was not ideal. The ramping fuel and coolant representation will be used in the final solution with some data being added between it to fill the large gap.

## Final decision on what will be used

For the final dash, there will be a number of display options available for use. This will display the different properties (Speed, RPM, Fuel, etc) on different screens. You will toggle between the screens using the buttons that are part of the dash. The final screen options that will appear in the final dash are as follows. The order is the order of which you can toggle through them. The last display option will be kept even after a power cycle so that you dod not need to toggle through all the options to get back to the one you wanted.

1) Settings panel - contains just text saying `Settings` centred on the screen. You will be able to select this page to enter the settings panel to adjust dash properties for calibration. This will use the [u8g2_font_5x7_mr](https://github.com/olikraus/u8g2/wiki/fntgrpx11#5x7) font to describe the settings available when you toggle through each page and the calibration instructions where appropriate. This font is used here as it will be used for other aspects of the dash. Reducing the amount of fonts used on the dash will reduce the storage requirement of the program allowing it to more likely fit onto the microcontroller.
2) Font based Speed Representation - This will be identical to the `font based speed representation` test. The speed numbers will be represented by the `u8g2_font_inr33_mn` font with the starting coordinates of X = 0 and Y = 32. The speed unit (kph or mph) will be represented by the `u8g2_font_t0_30_mr` font with the starting coordinates of X = 80 adn Y = 20. The trip/ odometer data will be represented by the `u8g2_font_5x7_mr` font with the starting coordinates X = 79 and Y = 32. There will be a toggle to cycle through the Odometer, Trip A and Trip B values using the dash buttons.
3) 32 High Segment based speed representation - This will use the 32 high segments in the `32 segment size test with trip and odometer` test. It will have a starting coordinate of X = 0 and Y = 32. The other data like speed unit (kph, mph) and trip/ odometer data will be identical to the setup in the font based speed version described in point 2 above.
4) Same RPM Representation - This will be nearly identical to the `RPM version a/1 test (Same)` version tested. It will use a bitmap to represent the RPM values at the top. The rpm bar will be represented/ generated using the [draw box](https://github.com/olikraus/u8g2/wiki/u8g2reference#drawbox) display class method. The odometer and trip data will be represented using the `u8g2_font_5x7_mr` font with the starting coordinates X = 0 and Y = 32.
5) Fuel and coolant ramping representation - This will be nearly identical to the `Coolant and fuel version a/1 test (Ramping)` version. It will use a bitmap to represent the coolant and fuel logos and will use the [draw box](https://github.com/olikraus/u8g2/wiki/u8g2reference#drawbox) display class method to represent each bar. The main additional aspect that was not included for the test will be the odometer and trip data all being displayed leftward between the coolant and fuel parts of the display but past the bar portions of both. The Odometer value will be at the bottom with trip B above it and trip A at the top all evenly spaced vertically using the `u8g2_font_5x7_mr` font.
T
Finally, separate to the main displays used in the dash. If there is enough storage on the microcontroller, I will add a startup graphics from my private library for fun. If there is not enough program storage I will not include the start up graphic.

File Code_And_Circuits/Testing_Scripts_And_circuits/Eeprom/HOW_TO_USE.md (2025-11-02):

# Eeprom Test for CBR dash project

This testing script is used to test the functionality of the external eeprom chip. The [CAT24C128](https://www.mouser.co.uk/ProductDetail/onsemi/CAT24C128WI-GT3?qs=rZgeL6XvLwaw%2FcBtNmrs8w%3D%3D) eeprom chip is used due to it being an I2C based eeprom chip and the similarity to the 512 Kbit version that is part of the [Sparkfun eeprom break out](https://www.sparkfun.com/sparkfun-qwiic-eeprom-breakout-512kbit.html). This gives a good code reference due to the [library and guide written](https://learn.sparkfun.com/tutorials/qwiic-eeprom-hookup-guide/all) for it. DFrobot have a similar [guide](https://wiki.dfrobot.com/Gravity__I2C_EEPROM_Data_Storage_Module_SKU__DFR0117#Connection%20Diagram) for their eeprom module which uses the same CAT24 eeprom chips that spark fun used. Both guides have been used as reference to create this test script and by effect the full dash code.

The test circuit is the V1 full PCB version with all components included due to the eeprom chip being SMD mounted.

Make sure to include the [sparkfun external eeprom I2C library](https://github.com/sparkfun/SparkFun_External_EEPROM_Arduino_Library/tree/main) in your project.

The script does a few things based on the serial input given to it to test the read and write functionality of the device. In the serial monitor the user is presented with a few options that do different things:

- 1 = Write an integer a user inputs to the first memory address.

- 2 = Read the integer in the first memory address

- 3 = Write a list of numbers into the eeprom starting with the 2nd aviable memory address.

- 4 = Read and find the highest number in the eeprom starting from the 2nd avaliable memory address.

Please note that memory address is dependant on the data types that come before it. For example an int takes 4 bytes (with an esp32 32 bit, 2 bytes with 16bit arduinos) while a float takes 4. Therefore, for an int in the first memory address the next avalaible memory address would be the 5th one (remember indexing starts at 0 thus memory index is 4 for 5th position).

## Why these features are tested

The features above are tested so that we are able to have precistant constantly undating data with the dash. Options 1 and 2 in the testing script is for testing the feasability of saving calibration data to the eeprom chip. Options 3 and 4 are for testing the ability to save odometer data into the eeprom. See the bellow note on odometer data problems.

## Important note on Odometer and trip meter data

Unlike most data that would be saved to this eeprom. Odometer and trip data constantly need to be updated very frequently. One concern is wear of the memory addresses if only one is used for each. Each address has a finite ammount of times it can be written to, thus constatly writting to one will make it fail very quickly. This can be mitigated by using a wear leveling stategy. Implementing this will help the eeprom chip to last longer.

For trip data, the last trip reset value n(when you reset the trip distance) will be retained in the eeprom. This means that the actual value will have to be calculated by comparing it to the current odometer reading. At the initial startup, the eeprom trip reset value will be read and compared against the odometer reading to give the trip value. This will be saved and updated in ram by the same ammount that the odometer reading is updated with. This allows less writes to the eeprom chip saving write lifes.

Odometer data is where wear leveling is nessary as the value must be imediatly saved to eeprom incase the bike suddenly shuts down thus, wear leveling is needed. The way this will work is by iterating over each memory address till the end of the addresses is reached. Once the last memory address is reached, it will return to the first address to continue the same process. This means that the writes are spread over many memory addresses leveling out the wear due to odometer readings. At startup, the memory addresses for the odometer data will be read. The highest value and it's position will be loaded into RAM so that the dash has accurate odometer readings and knows the last location it wrote to. For each increase of 0.1Km the odometer reading will be captured in eeprom. The start memory address for this is dependent on how much memory is required for calibration data for the dash. Similarly the end memory address is dependent on the size of the data type that needs to be written and the size of the eeprom chip. For example, we can write to memory addresses 0 to 9 where each address is a byte (8 bits,10 bytes worth of memory). Assume there is no static data and it is just odometer data. Asssume we are using floats to hold odometer data (4 bytes). We can start at memory address 0 then write to address 4 (first value sits in addresses 0-3, secound in 4-7). Even though we have addresses 8 and 9. We are unable to write to them as we need two more bytes to write the full float value.

Odometer data will be an integer to avoid errors with floating point math. For esp32s they work on 32bit microprocessors meaning that ints are 32 bits instead of the typical 16 bits in arduino. This means that the max int value is 2,147,483,647. This is plenty high enough for an odometer reading if using my ideal unit of Km. The dash will use all SI units for data and convert when displaying data. It must be noted that the first value of the int will represent the 0.1 of a kilometer (100 meters). Everytime the odometer reading updates by that 0.1Km it will be saved to eeprom to reduce writes. At run time, a separate variable will keep track of how much distance has been traveled and once it reaches the 0.1km threshold it will trigger an odomeeer reading update. It will then reset it's self back to 0 to get back to that 0.1km threashold. The exact unit it will use is still to be decided as of writting (could be cm to stick to int math or it could be m to use floating point math). This will clearly lead to the odometer reading being a bit lower than the actual distance traveled but for my use case that is ok. It will also negate any addition problems with floating point math if it is used.

This test script will contain a calculation to find the last memory address it can write for options 3 and 4.

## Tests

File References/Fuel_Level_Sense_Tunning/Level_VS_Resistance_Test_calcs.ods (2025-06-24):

 |  |  |  |  |  | Assuming linear relationship between bottom and top
Pot(Ohm) | Ra(Ohm) | Rb(Ohm) | Leg(A)(V) | Leg(B)(V) | How far Actually (%Full) | Predicted(A) | Predicted(B) | Average of A + B | Difference In Predicted and Actual For Leg A | Difference In Predicted and Actual For Leg B | Difference_In_Predicted_And_Actual_for_Average
33 | 33 | 567 | 0.287512100677638 | 3.25654116145501 | 0.00% | 0.00% | 0.00% | 0.00% | 0.00% | 0.00% | 0.00%
35 | 35 | 565 | 0.304347826086957 | 3.24920127795527 | 0.38% | 0.57% | 0.25% | 0.41% | -0.19% | 0.13% | -0.03%
40 | 40 | 560 | 0.346153846153846 | 3.23076923076923 | 1.31% | 1.98% | 0.87% | 1.42% | -0.66% | 0.44% | -0.11%
60 | 60 | 540 | 0.509433962264151 | 3.15584415584416 | 5.07% | 7.48% | 3.40% | 5.44% | -2.42% | 1.66% | -0.38%
80 | 80 | 520 | 0.666666666666667 | 3.07894736842105 | 8.82% | 12.79% | 6.00% | 9.39% | -3.97% | 2.82% | -0.57%
100 | 100 | 500 | 0.818181818181818 | 3 | 12.57% | 17.90% | 8.67% | 13.28% | -5.33% | 3.91% | -0.71%
120 | 120 | 480 | 0.964285714285714 | 2.91891891891892 | 16.32% | 22.82% | 11.40% | 17.11% | -6.50% | 4.92% | -0.79%
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

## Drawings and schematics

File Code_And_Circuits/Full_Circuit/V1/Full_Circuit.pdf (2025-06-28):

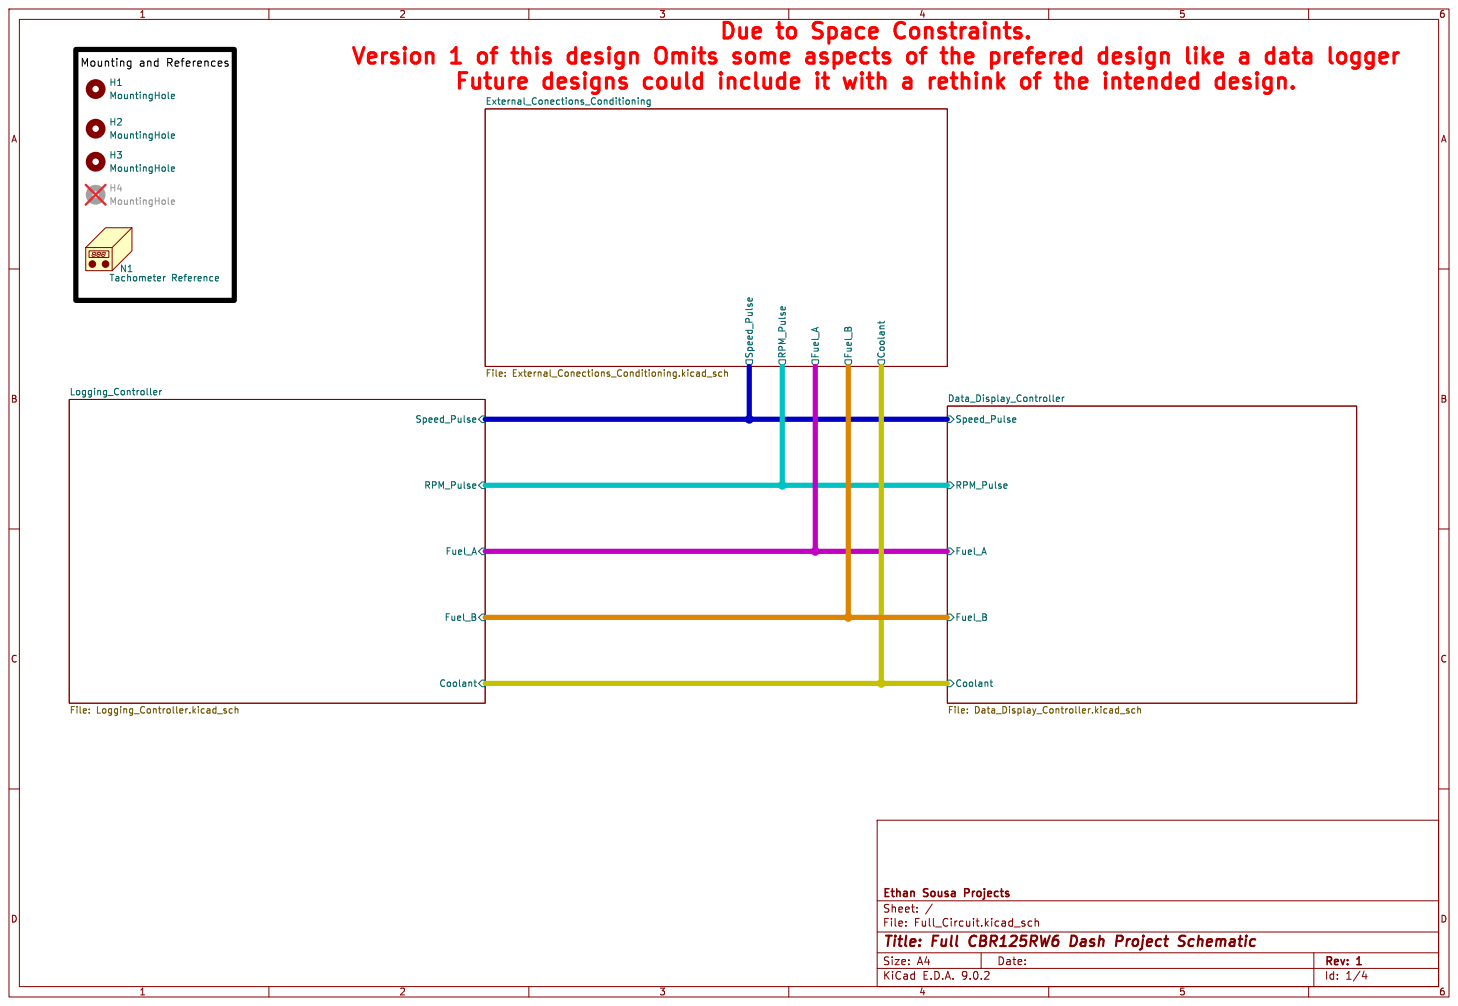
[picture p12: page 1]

Future designs could include it with a rethink of the intended design.

Id: 1/4 Title: Full CBR125RW6 Dash Project Schematic

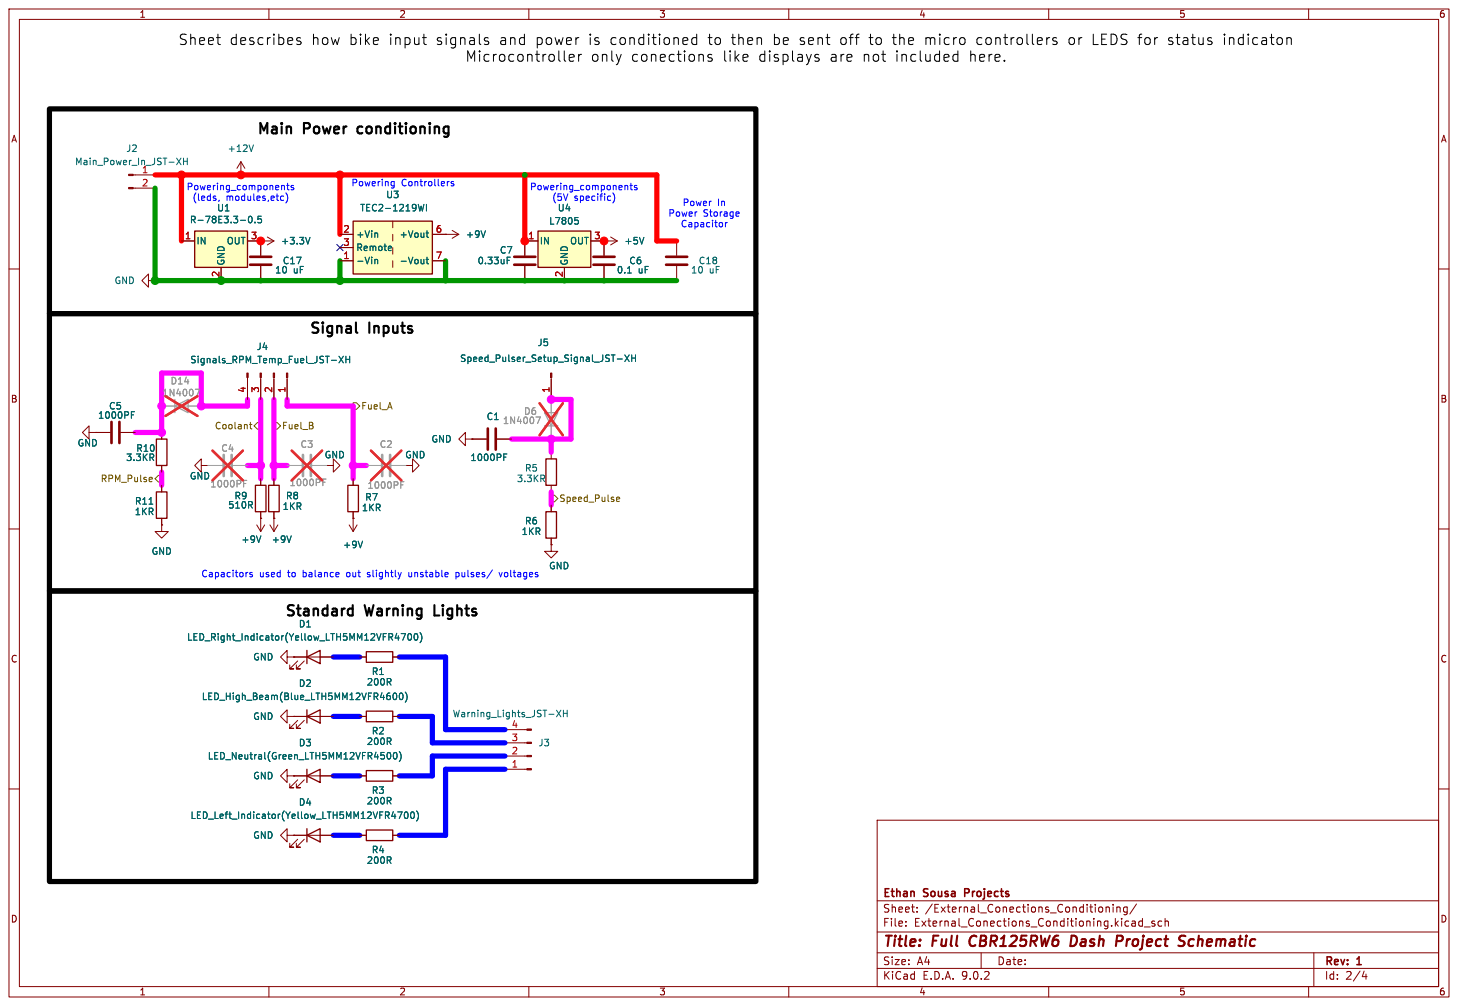
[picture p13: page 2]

Powering Controllers Standard Warning Lights

Power In Power Storage

Id: 2/4 Title: Full CBR125RW6 Dash Project Schematic

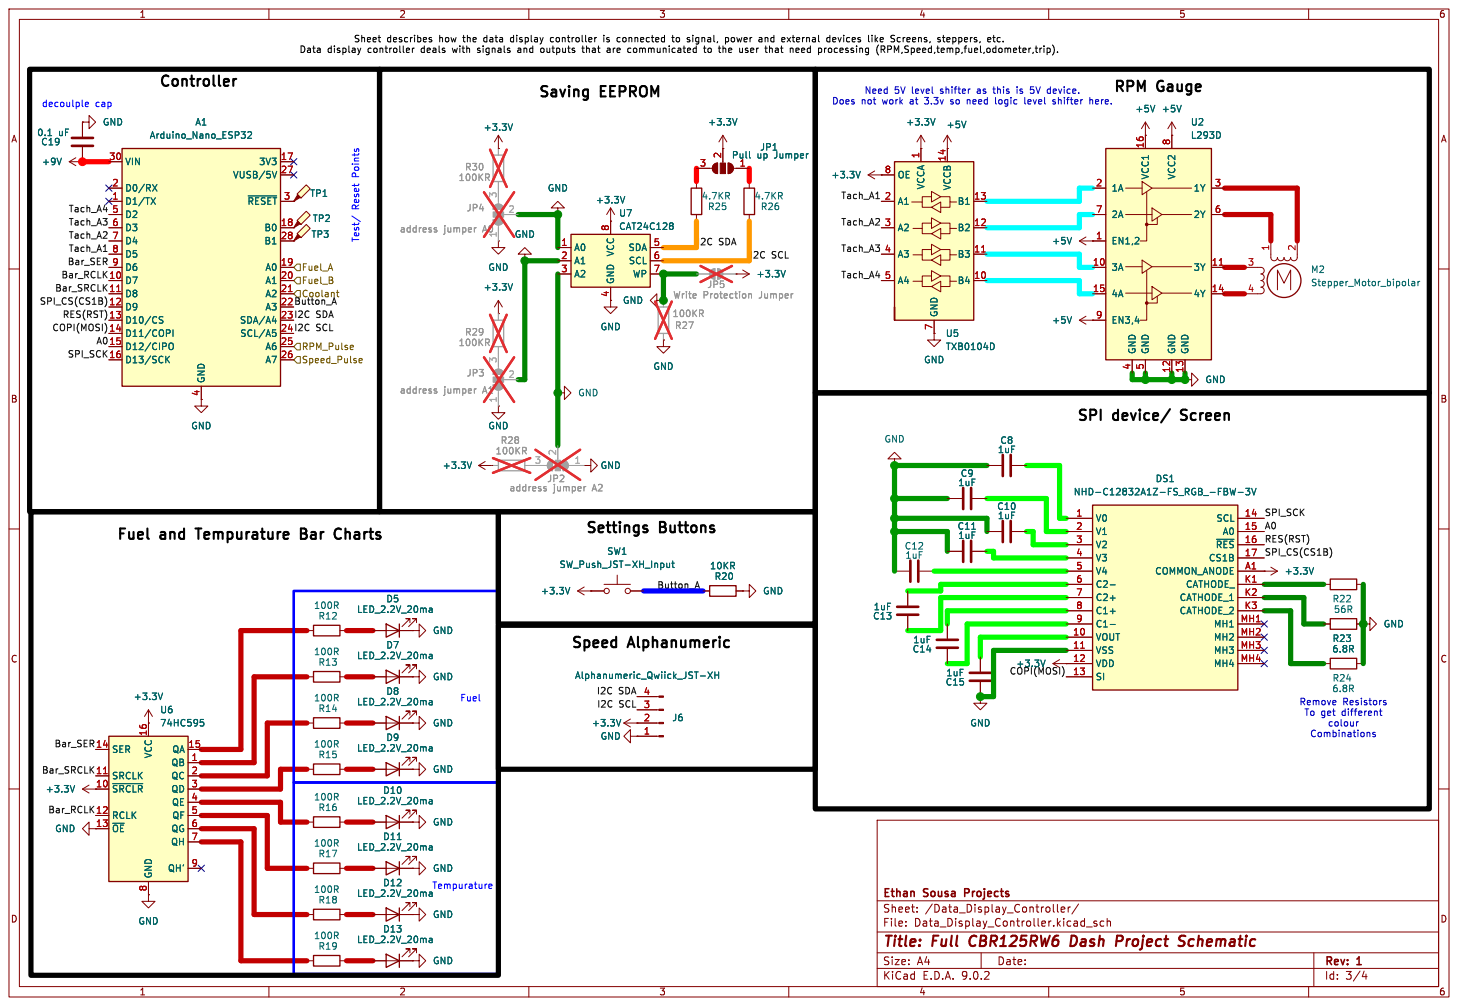
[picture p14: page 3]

3V3 17 VUSB/5V 27 ~{RESET}3 B0 18 B1 28 A0 19 A1 20 A2 21 A3 22 SDA/A4 23 SCL/A5 24 A6 25 A7 26 A1 Arduino_Nano_ESP32 C19
+3.3V GND
3V3 17 VUSB/5V 27 ~{RESET}3 B0 18 B1 28 A0 19 A1 20 A2 21 A3 22 SDA/A4 23 SCL/A5 24 A6 25 A7 26 C19

4 SDA 5 SCL 6 WP 7 U7 CAT24C128 GND

8 QA 15 QB 1 QC 2 QD 3 QE 4 QF 5 QG 6 QH 7 QH' 9 GND

J6 Alphanumeric_Qwiick_JST-XH GND GND GND

Fuel and Tempurature Bar Charts

Remove Resistors To get different colour Combinations

Id: 3/4 Title: Full CBR125RW6 Dash Project Schematic

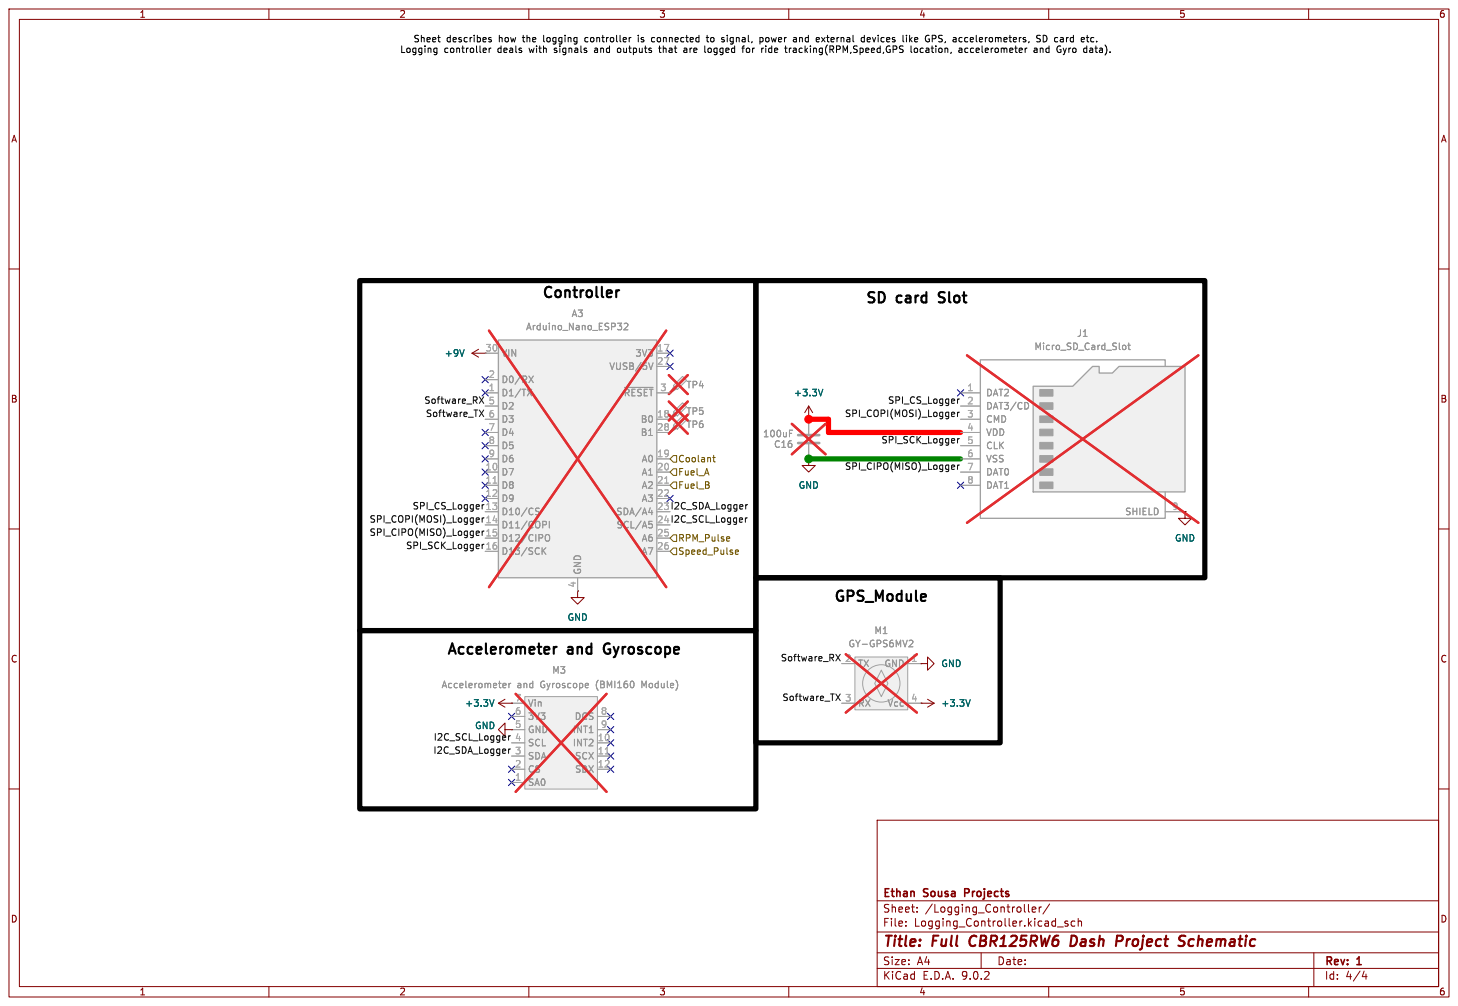
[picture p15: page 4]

Id: 4/4 Title: Full CBR125RW6 Dash Project Schematic

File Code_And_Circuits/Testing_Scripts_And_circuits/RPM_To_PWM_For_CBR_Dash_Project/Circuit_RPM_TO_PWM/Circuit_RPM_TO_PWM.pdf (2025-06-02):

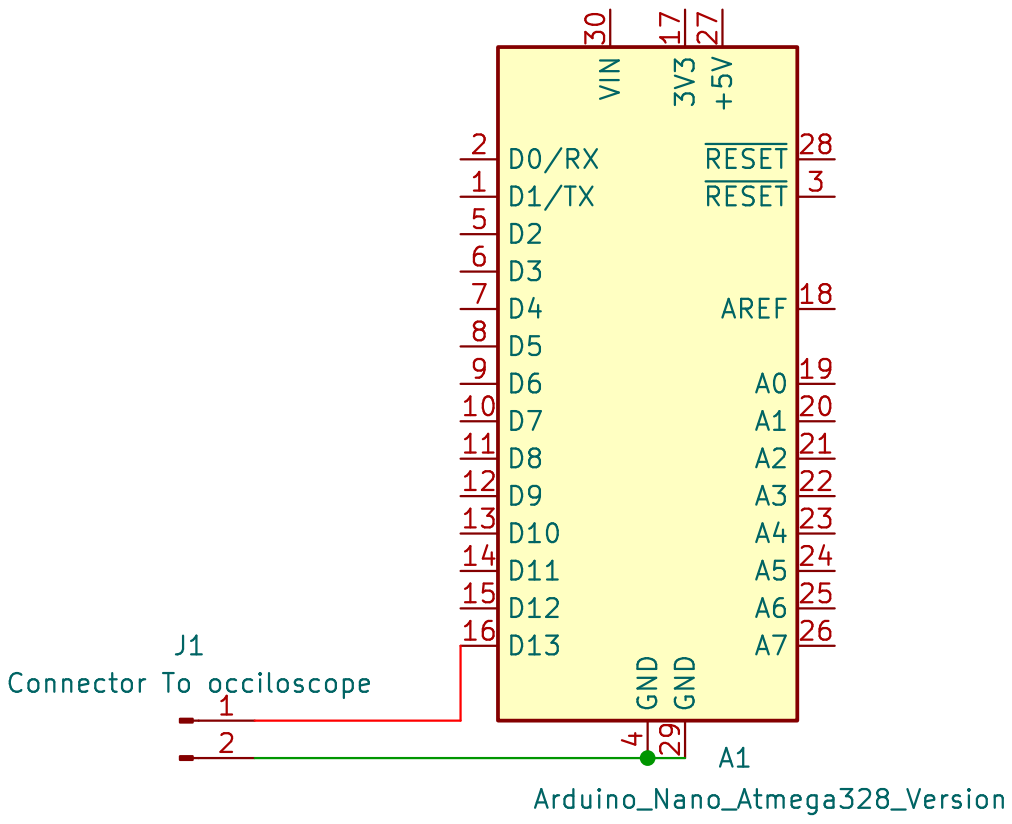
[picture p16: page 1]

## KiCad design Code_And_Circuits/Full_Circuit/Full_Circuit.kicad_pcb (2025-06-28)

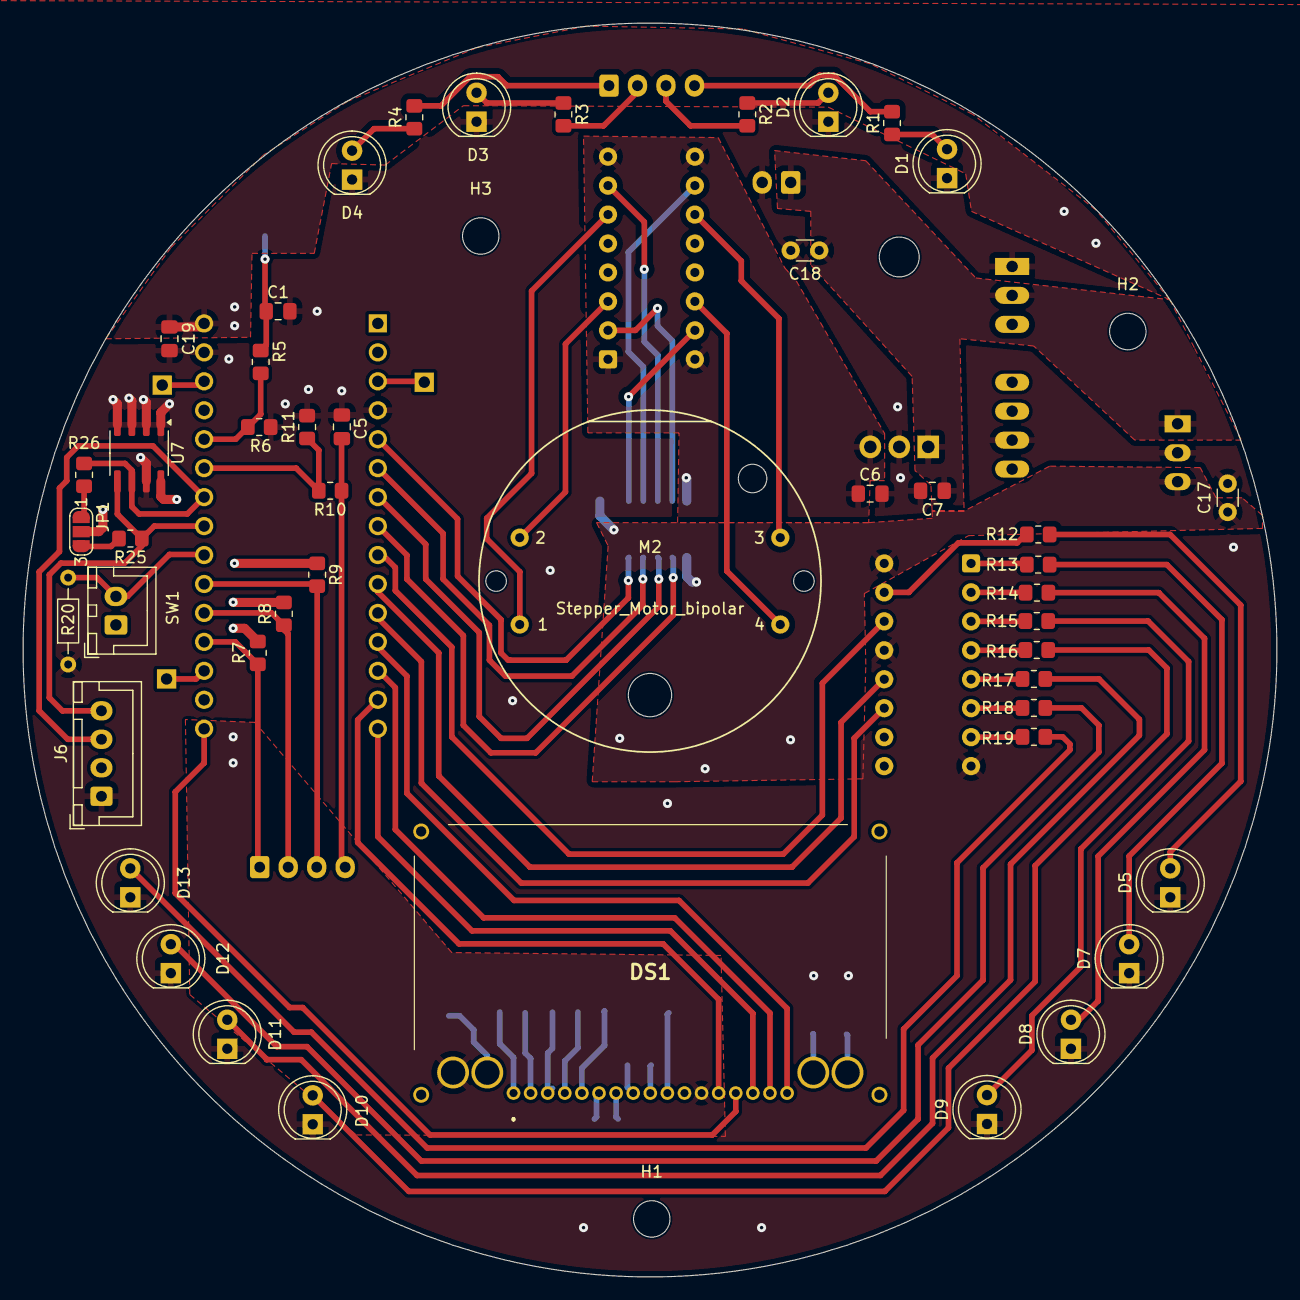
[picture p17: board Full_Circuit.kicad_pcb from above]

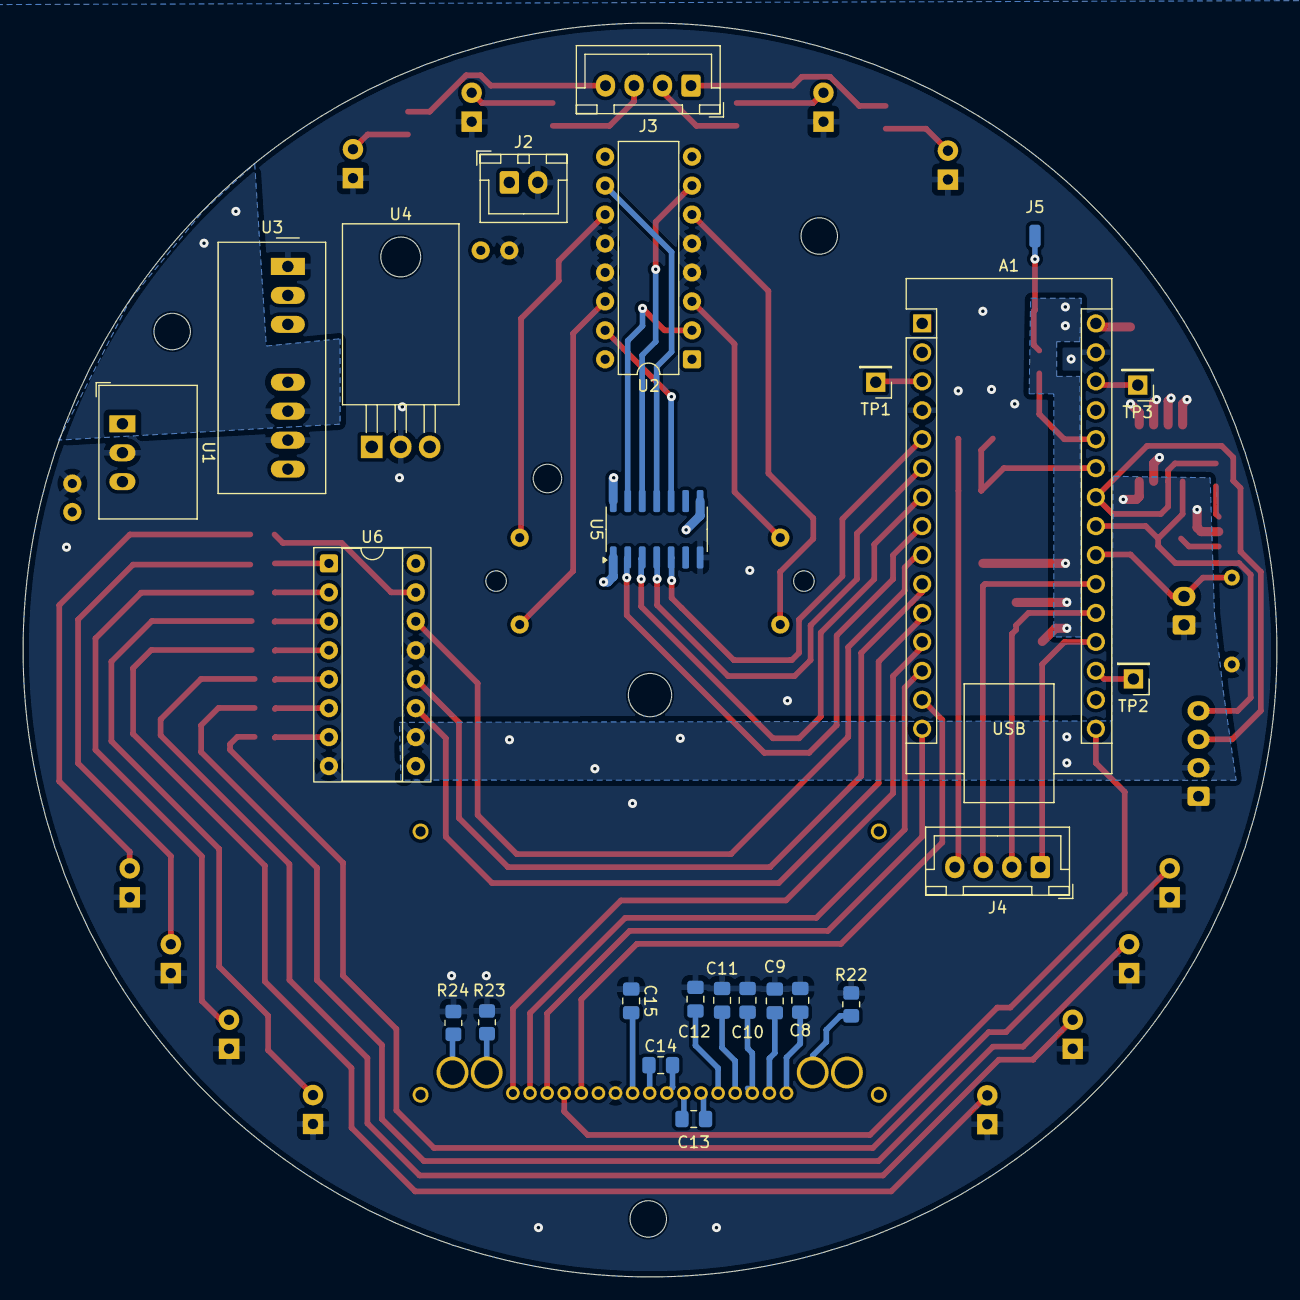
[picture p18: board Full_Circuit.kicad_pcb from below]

Board: 2 copper layers, 110.0 x 110.0 mm, 76 parts (25 on the bottom side), 77 nets.

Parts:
A1: Arduino_Nano_ESP32; Arduino_Nano
C1, C5: 1000PF; C_0805_2012Metric_Pad1.18x1.45mm_HandSolder
C6, C19: 0.1 uF; C_0805_2012Metric_Pad1.18x1.45mm_HandSolder
C7: 0.33uF; C_0805_2012Metric_Pad1.18x1.45mm_HandSolder
C8, C9, C10, C11, C12, C13, C14, C15: 1uF; C_0805_2012Metric_Pad1.18x1.45mm_HandSolder
C17, C18: 10 uF; C_Disc_D3.0mm_W1.6mm_P2.50mm
D1: LED_Right_Indicator(Yellow_LTH5MM12VFR4700); LED_D5.0mm
D2: LED_High_Beam(Blue_LTH5MM12VFR4600); LED_D5.0mm
D3: LED_Neutral(Green_LTH5MM12VFR4500); LED_D5.0mm
D4: LED_Left_Indicator(Yellow_LTH5MM12VFR4700); LED_D5.0mm
D5, D7, D8, D9, D10, D11, D12, D13: LED_2.2V_20ma; LED_D5.0mm
DS1: NHD-C12832A1Z-FS_RGB_-FBW-3V; NHDC12832A1ZFSRGBFBW3V
H1, H2, H3: MountingHole; MountingHole_3.2mm_M3
J2: Main_Power_In_JST-XH; JST_XH_B2B-XH-A_1x02_P2.50mm_Vertical
J3: Warning_Lights_JST-XH; JST_XH_B4B-XH-A_1x04_P2.50mm_Vertical
J4: Signals_RPM_Temp_Fuel_JST-XH; JST_XH_B4B-XH-A_1x04_P2.50mm_Vertical
J5: Speed_Pulser_Setup_Signal_JST-XH; SolderWirePad_1x01_SMD_1x2mm
J6: Alphanumeric_Qwiick_JST-XH; JST_XH_B4B-XH-A_1x04_P2.50mm_Vertical
JP1: Pull up Jumper; SolderJumper-3_P1.3mm_Open_RoundedPad1.0x1.5mm_NumberLabels
M2: Stepper_Motor_bipolar; X27-168
N1: Tachometer Reference; Dial_Gauge_Reference_CBF600
R1, R2, R3, R4: 200R; R_0805_2012Metric_Pad1.20x1.40mm_HandSolder
R5, R10: 3.3KR; R_0805_2012Metric_Pad1.20x1.40mm_HandSolder
R6, R7, R8, R11: 1KR; R_0805_2012Metric_Pad1.20x1.40mm_HandSolder
R9: 510R; R_0805_2012Metric_Pad1.20x1.40mm_HandSolder
R12, R13, R14, R15, R16, R17, R18, R19: 100R; R_0805_2012Metric_Pad1.20x1.40mm_HandSolder
R20: 10KR; R_Axial_DIN0204_L3.6mm_D1.6mm_P7.62mm_Horizontal
R22: 56R; R_0805_2012Metric_Pad1.20x1.40mm_HandSolder
R23, R24: 6.8R; R_0805_2012Metric_Pad1.20x1.40mm_HandSolder
R25, R26: 4.7KR; R_0805_2012Metric_Pad1.20x1.40mm_HandSolder
SW1: SW_Push_JST-XH_Input; JST_XH_B2B-XH-A_1x02_P2.50mm_Vertical
TP1, TP2, TP3: TestPoint; PinHeader_1x01_P2.54mm_Vertical
U1: R-78E3.3-0.5; Converter_DCDC_RECOM_R-78E-0.5_THT
U2: L293D; DIP-16_W7.62mm
U3: TEC2-1219WI; Converter_DCDC_TRACO_TMR-xxxx_THT
U4: L7805; TO-220-3_Horizontal_TabDown
U5: TXB0104D; SOIC-14_3.9x8.7mm_P1.27mm
U6: 74HC595; DIP-16_W7.62mm_Socket
U7: CAT24C128; SOIC-8_3.9x4.9mm_P1.27mm

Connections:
+3.3V: C17.1, DS1.12 (VDD), DS1.A1 (COMMON_ANODE), J6.2, JP1.2 (C), SW1.1, U1.3 (OUT), U5.1 (VCCA), U5.8 (OE), U6.10 (~SRCLR), U6.16 (VCC), U7.8 (VCC)
+5V: C6.1, U2.1 (EN1,2), U2.8 (VCC2), U2.9 (EN3,4), U2.16 (VCC1), U4.3 (OUT), U5.14 (VCCB)
+9V: A1.30 (VIN), C19.1, R7.2, R8.2, R9.1, U3.6 (+Vout)
+12V: C7.1, C18.1, J2.1, U1.1 (IN), U3.2 (+Vin), U4.1 (IN)
/Data_Display_Controller/A0: A1.15 (D12/CIPO), DS1.15 (A0)
/Data_Display_Controller/Bar_RCLK: A1.10 (D7), U6.12 (RCLK)
/Data_Display_Controller/Bar_SER: A1.9 (D6), U6.14 (SER)
/Data_Display_Controller/Bar_SRCLK: A1.11 (D8), U6.11 (SRCLK)
/Data_Display_Controller/Button_A: A1.22 (A3), R20.2, SW1.2
/Data_Display_Controller/COPI(MOSI): A1.14 (D11/COPI), DS1.13 (SI)
/Data_Display_Controller/Coolant: A1.21 (A2), J4.3, R9.2
/Data_Display_Controller/Fuel_A: A1.19 (A0), J4.1, R7.1
/Data_Display_Controller/Fuel_B: A1.20 (A1), J4.2, R8.1
/Data_Display_Controller/I2C SCL: A1.24 (SCL/A5), J6.3, R26.1, U7.6 (SCL)
/Data_Display_Controller/I2C SDA: A1.23 (SDA/A4), J6.4, R25.1, U7.5 (SDA)
/Data_Display_Controller/RES(RST): A1.13 (D10/CS), DS1.16 (~RES)
/Data_Display_Controller/RPM_Pulse: A1.25 (A6), R10.2, R11.1
/Data_Display_Controller/SPI_CS(CS1B): A1.12 (D9), DS1.17 (CS1B)
/Data_Display_Controller/SPI_SCK: A1.16 (D13/SCK), DS1.14 (SCL)
/Data_Display_Controller/Speed_Pulse: A1.26 (A7), R5.2, R6.1
/Data_Display_Controller/Tach_A1: A1.8 (D5), U5.2 (A1)
/Data_Display_Controller/Tach_A2: A1.7 (D4), U5.3 (A2)
/Data_Display_Controller/Tach_A3: A1.6 (D3), U5.4 (A3)
/Data_Display_Controller/Tach_A4: A1.5 (D2), U5.5 (A4)
GND: A1.4 (GND), A1.29 (GND), C1.2, C5.1, C6.2, C7.2, C8.1, C9.1, C10.1, C11.1, C12.1, C15.1, C17.2, C18.2, C19.2, D1.1 (K), D2.1 (K), D3.1 (K), D4.1 (K), D5.1 (K), D7.1 (K), D8.1 (K), D9.1 (K), D10.1 (K), D11.1 (K), D12.1 (K), D13.1 (K), DS1.11 (VSS), J2.2, J6.1, R6.2, R11.2, R20.1, R22.2, R23.2, R24.2, U1.2 (GND), U2.4 (GND), U2.5 (GND), U2.12 (GND), U2.13 (GND), U3.1 (-Vin), U3.7 (-Vout), U4.2 (GND), U5.7 (GND), U6.8 (GND), U6.13 (~OE), U7.1 (A0), U7.2 (A1), U7.3 (A2), U7.4 (GND), U7.7 (WP)
unnamed: A1.18 (B0), TP2.1
unnamed: A1.28 (B1), TP3.1
unnamed: A1.3 (~RESET), TP1.1
unnamed: D1.2 (A), R1.1
unnamed: D2.2 (A), R2.1
unnamed: D3.2 (A), R3.1
unnamed: D4.2 (A), R4.1
unnamed: D5.2 (A), R12.1
unnamed: D7.2 (A), R13.1
unnamed: D8.2 (A), R14.1
unnamed: D9.2 (A), R15.1
unnamed: D10.2 (A), R16.1
unnamed: D11.2 (A), R17.1
unnamed: D12.2 (A), R18.1
unnamed: D13.2 (A), R19.1
unnamed: C14.2, DS1.8 (C1+)
unnamed: C14.1, DS1.9 (C1-)
unnamed: C13.1, DS1.7 (C2+)
unnamed: C13.2, DS1.6 (C2-)
unnamed: DS1.K2 (CATHODE_1), R23.1
unnamed: DS1.K3 (CATHODE_2), R24.1
unnamed: DS1.K1 (CATHODE_), R22.1
unnamed: C8.2, DS1.1 (V0)
unnamed: C9.2, DS1.2 (V1)
unnamed: C10.2, DS1.3 (V2)
unnamed: C11.2, DS1.4 (V3)
unnamed: C12.2, DS1.5 (V4)
unnamed: C15.2, DS1.10 (VOUT)
unnamed: J3.1, R4.2
unnamed: J3.2, R3.2
unnamed: J3.3, R2.2
unnamed: J3.4, R1.2
unnamed: C5.2, J4.4, R10.1
unnamed: C1.1, J5.1, R5.1
unnamed: JP1.1 (A), R26.2
unnamed: JP1.3 (B), R25.2
unnamed: M2.2 (-), U2.3 (1Y)
unnamed: U2.2 (1A), U5.13 (B1)
unnamed: U2.7 (2A), U5.12 (B2)
unnamed: M2.1, U2.6 (2Y)
unnamed: U2.10 (3A), U5.11 (B3)
unnamed: M2.3, U2.11 (3Y)
unnamed: U2.15 (4A), U5.10 (B4)
unnamed: M2.4, U2.14 (4Y)
unnamed: R12.2, U6.15 (QA)
unnamed: R13.2, U6.1 (QB)
unnamed: R14.2, U6.2 (QC)
unnamed: R15.2, U6.3 (QD)
unnamed: R16.2, U6.4 (QE)
unnamed: R17.2, U6.5 (QF)
unnamed: R18.2, U6.6 (QG)
unnamed: R19.2, U6.7 (QH)

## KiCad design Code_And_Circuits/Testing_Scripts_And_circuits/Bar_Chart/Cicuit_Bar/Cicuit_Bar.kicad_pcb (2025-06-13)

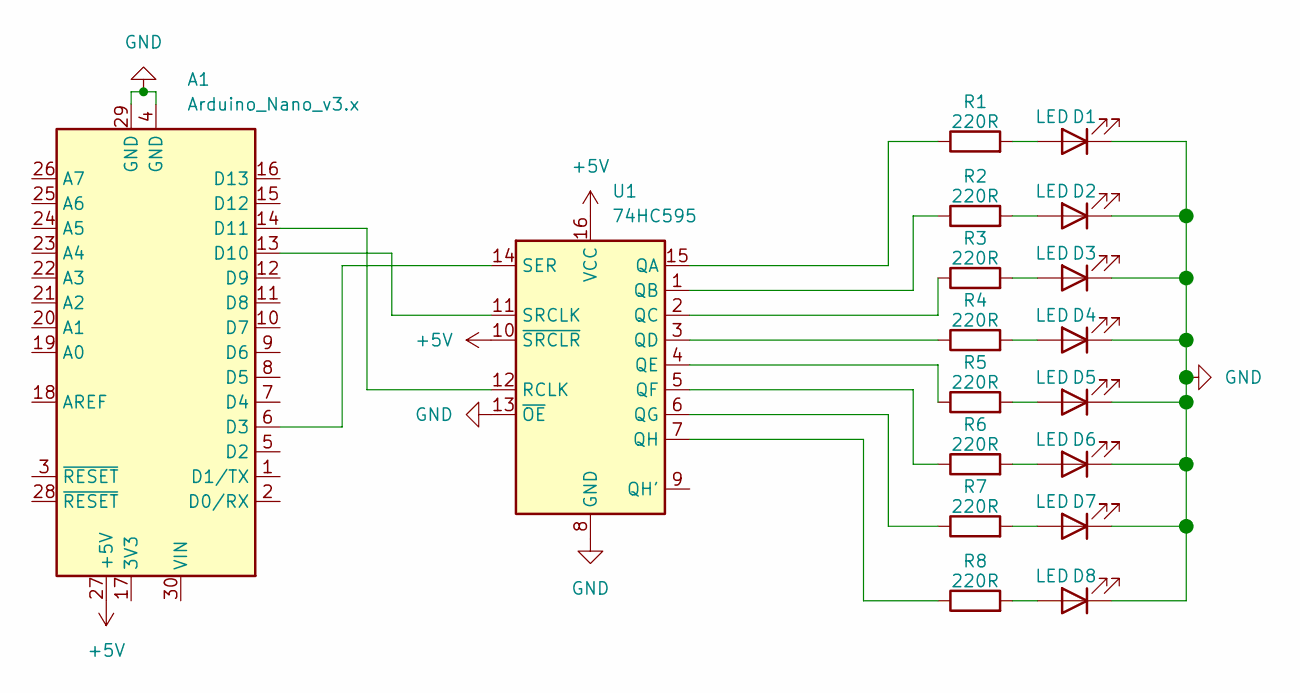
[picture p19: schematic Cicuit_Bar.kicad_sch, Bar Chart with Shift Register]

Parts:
A1: Arduino_Nano_v3.x; Arduino_Nano
D1, D2, D3, D4, D5, D6, D7, D8: LED; LED_D5.0mm
R1, R2, R3, R4, R5, R6, R7, R8: 220R; R_Axial_DIN0204_L3.6mm_D1.6mm_P7.62mm_Horizontal
U1: 74HC595; DIP-16_W7.62mm_Socket

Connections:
+5V: A1.27 (+5V), U1.10 (~SRCLR), U1.16 (VCC)
GND: A1.4 (GND), A1.29 (GND), D1.1 (K), D2.1 (K), D3.1 (K), D4.1 (K), D5.1 (K), D6.1 (K), D7.1 (K), D8.1 (K), U1.8 (GND), U1.13 (~OE)
unnamed: A1.6 (D3), U1.14 (SER)
unnamed: A1.13 (D10), U1.11 (SRCLK)
unnamed: A1.14 (D11), U1.12 (RCLK)
unnamed: D1.2 (A), R1.2
unnamed: D2.2 (A), R2.2
unnamed: D3.2 (A), R3.2
unnamed: D4.2 (A), R4.2
unnamed: D5.2 (A), R5.2
unnamed: D6.2 (A), R6.2
unnamed: D7.2 (A), R7.2
unnamed: D8.2 (A), R8.2
unnamed: R1.1, U1.15 (QA)
unnamed: R2.1, U1.1 (QB)
unnamed: R3.1, U1.2 (QC)
unnamed: R4.1, U1.3 (QD)
unnamed: R5.1, U1.4 (QE)
unnamed: R6.1, U1.5 (QF)
unnamed: R7.1, U1.6 (QG)
unnamed: R8.1, U1.7 (QH)

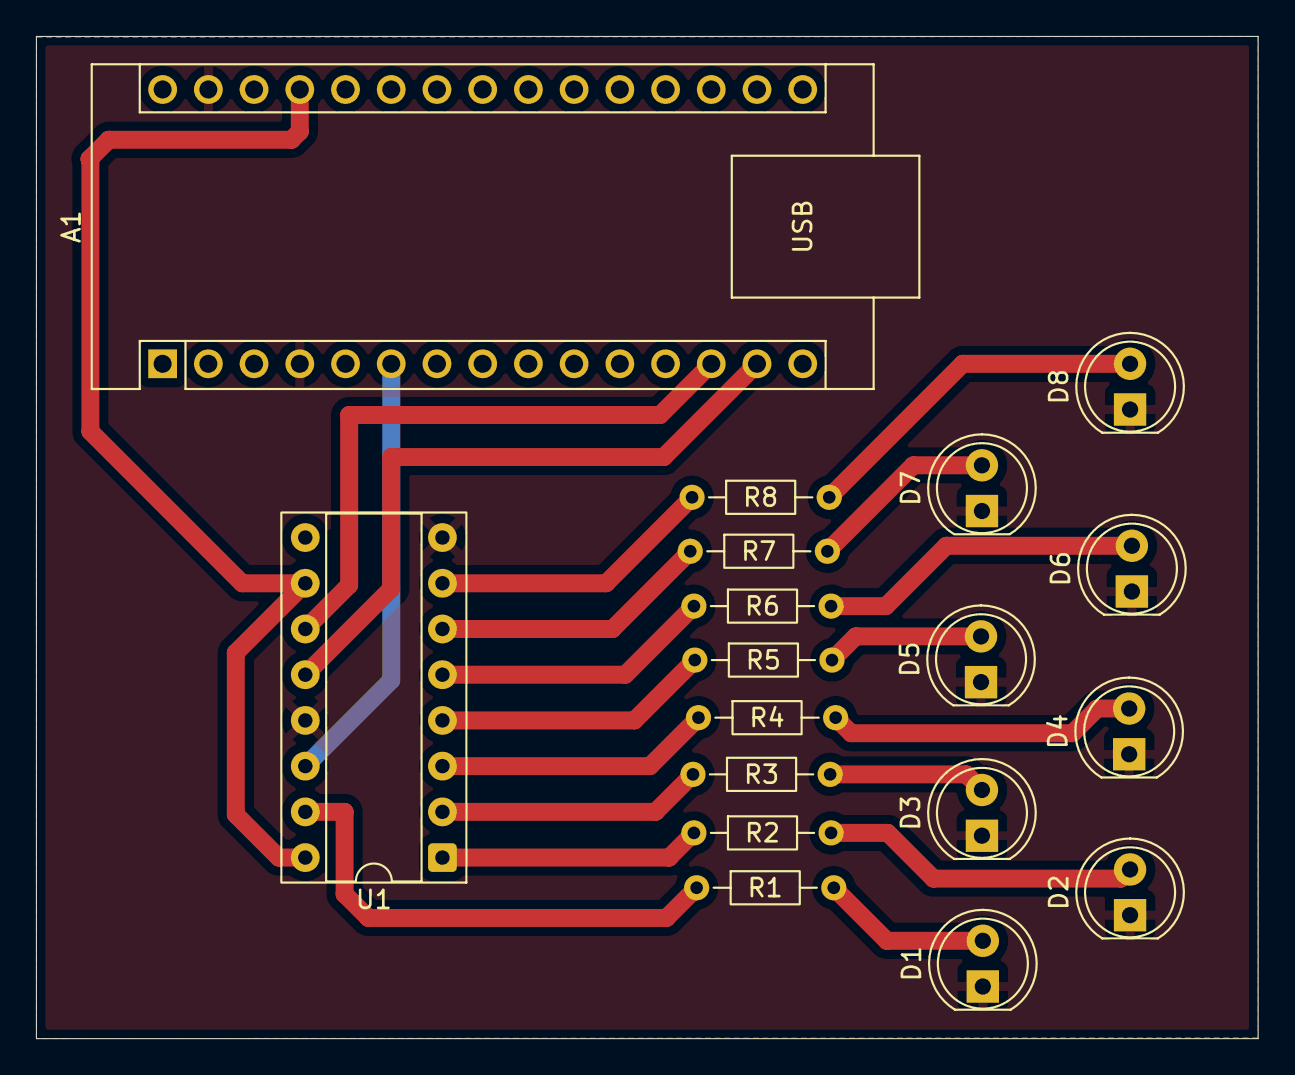
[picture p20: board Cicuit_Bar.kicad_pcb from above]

Board: 2 copper layers, 67.9 x 55.7 mm, 18 parts (0 on the bottom side), 21 nets.

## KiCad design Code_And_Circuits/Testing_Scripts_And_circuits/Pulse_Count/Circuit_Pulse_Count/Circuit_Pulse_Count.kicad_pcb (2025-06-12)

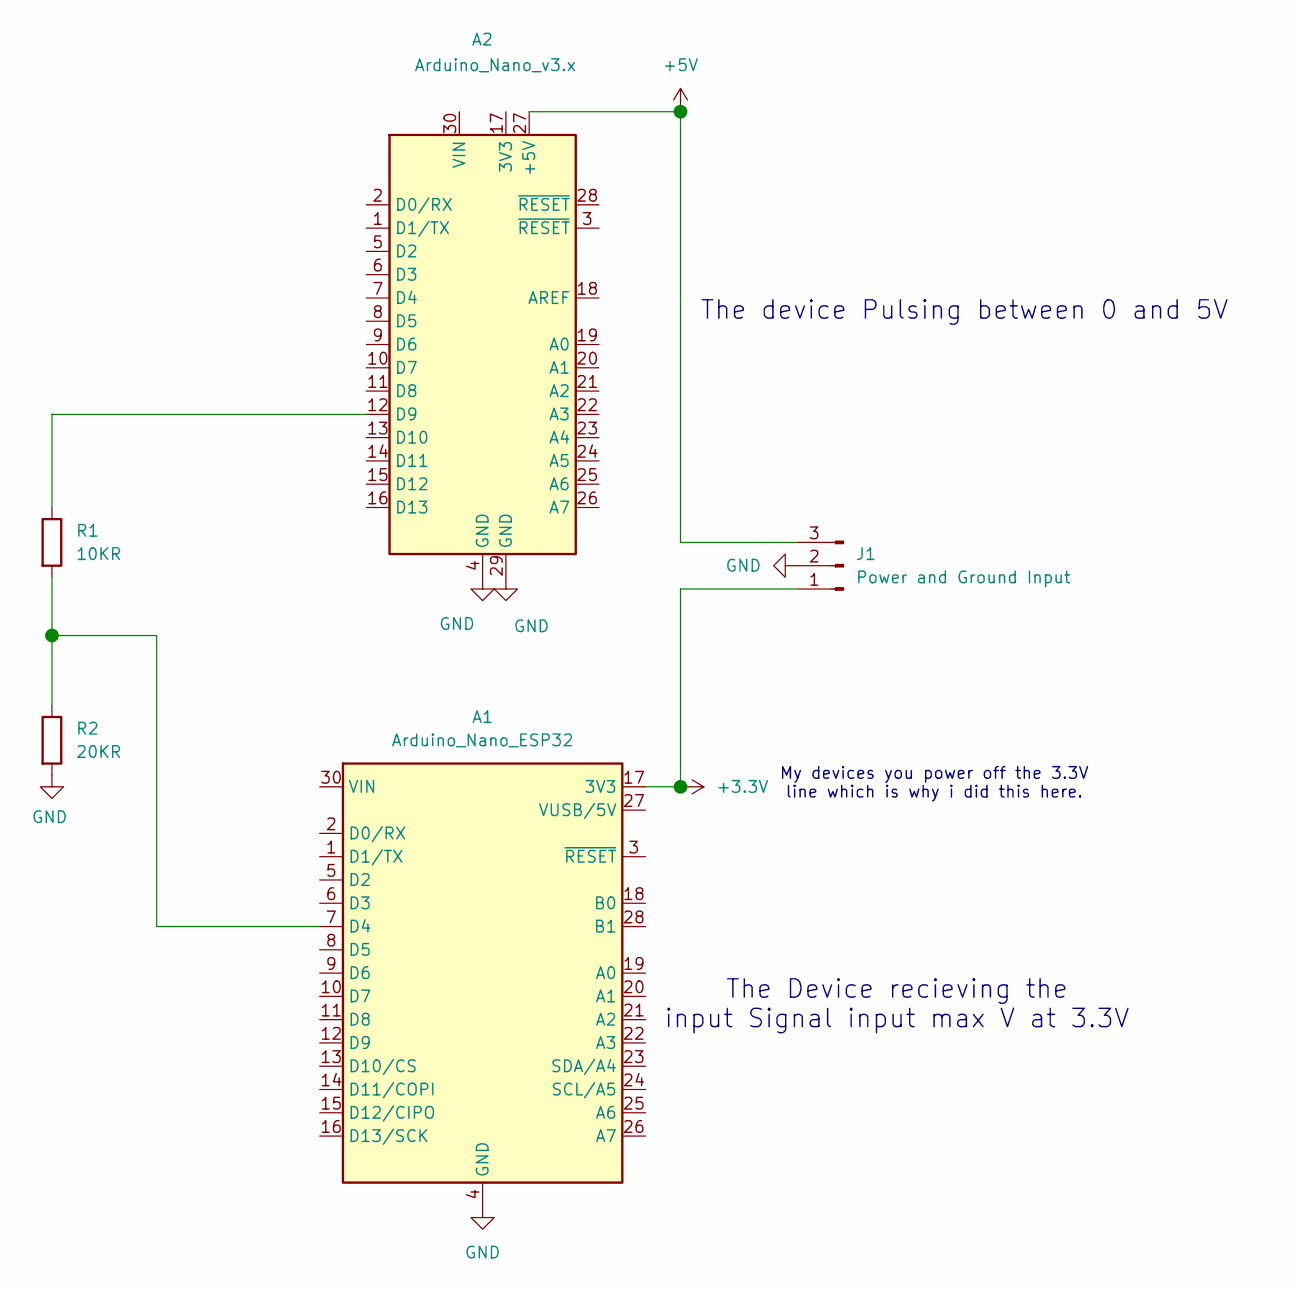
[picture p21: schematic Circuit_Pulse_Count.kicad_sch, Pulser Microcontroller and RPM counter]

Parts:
A1: Arduino_Nano_ESP32; Arduino_Nano
A2: Arduino_Nano_v3.x; Arduino_Nano
J1: Power and Ground Input; PinHeader_1x03_P2.54mm_Vertical
R1: 10KR; R_Axial_DIN0204_L3.6mm_D1.6mm_P7.62mm_Horizontal
R2: 20KR; R_Axial_DIN0204_L3.6mm_D1.6mm_P7.62mm_Horizontal

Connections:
+3.3V: A1.17 (3V3), J1.1
+5V: A2.27 (+5V), J1.3
GND: A1.4 (GND), A1.29 (GND), A2.4 (GND), A2.29 (GND), J1.2, R2.2
unnamed: A1.7 (D4), R1.2, R2.1
unnamed: A2.12 (D9), R1.1

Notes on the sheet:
The device Pulsing between 0 and 5V
My devices you power off the 3.3V line which is why i did this here.
The Device recieving the input Signal input max V at 3.3V

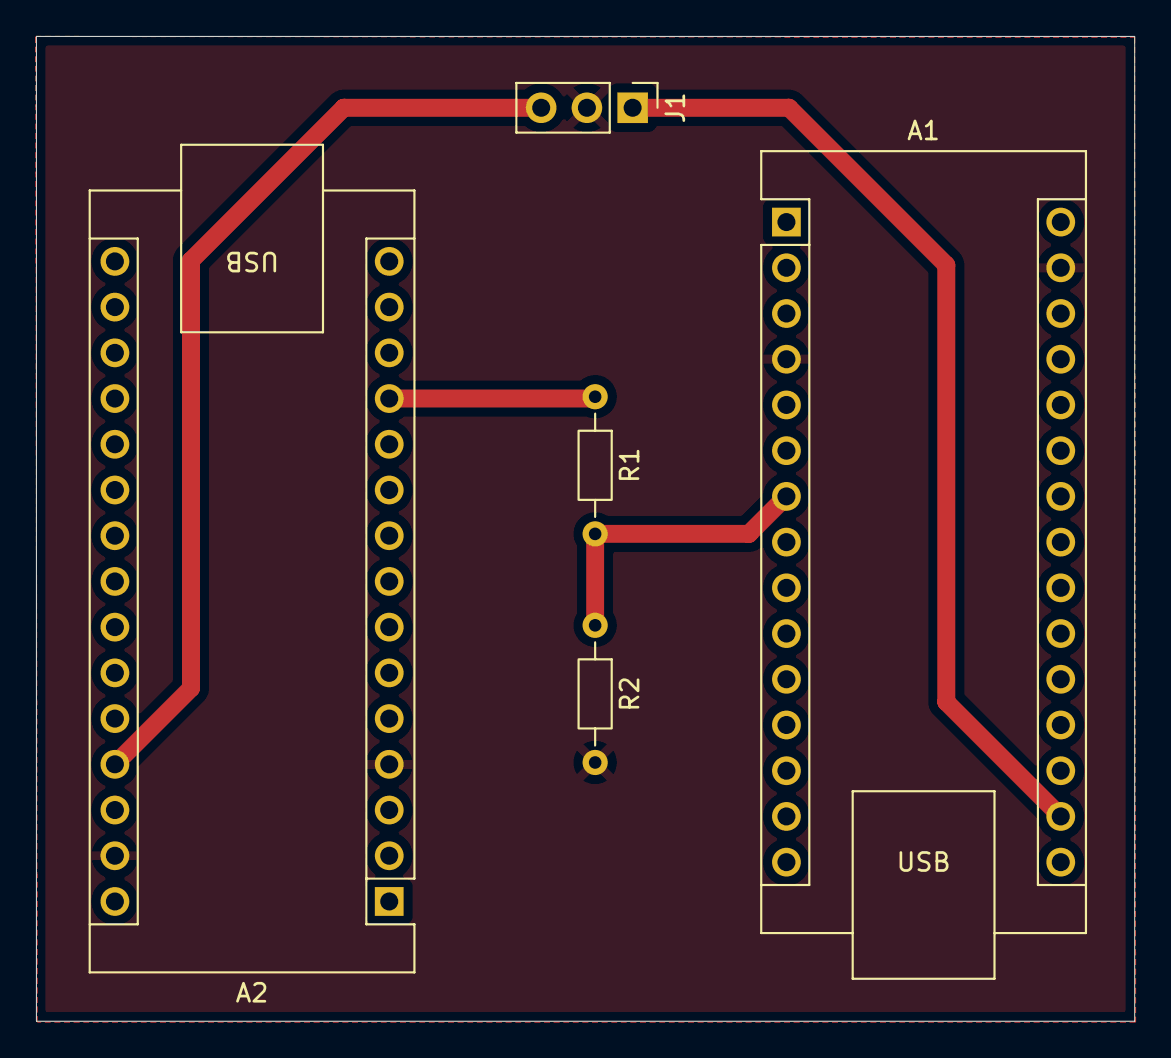
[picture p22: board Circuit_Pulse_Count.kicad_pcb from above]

Board: 2 copper layers, 61.0 x 54.7 mm, 5 parts (0 on the bottom side), 5 nets.

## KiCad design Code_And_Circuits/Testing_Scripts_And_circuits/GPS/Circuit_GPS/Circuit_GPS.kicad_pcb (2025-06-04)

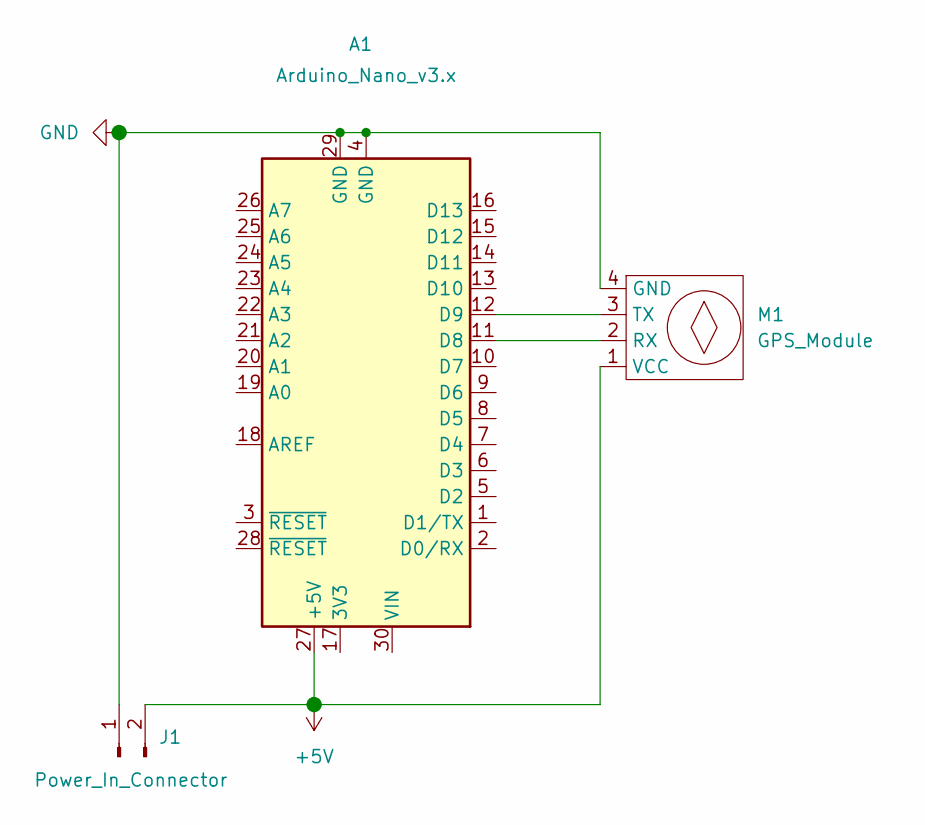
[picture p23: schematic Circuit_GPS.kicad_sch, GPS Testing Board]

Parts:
A1: Arduino_Nano_v3.x; Arduino_Nano
J1: Power_In_Connector; PinHeader_1x02_P2.54mm_Vertical
M1: GPS_Module; PinSocket_1x04_P2.54mm_Vertical

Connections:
+5V: A1.27 (+5V), J1.2, M1.1 (VCC)
GND: A1.4 (GND), A1.29 (GND), J1.1, M1.4 (GND)
unnamed: A1.11 (D8), M1.2 (RX)
unnamed: A1.12 (D9), M1.3 (TX)

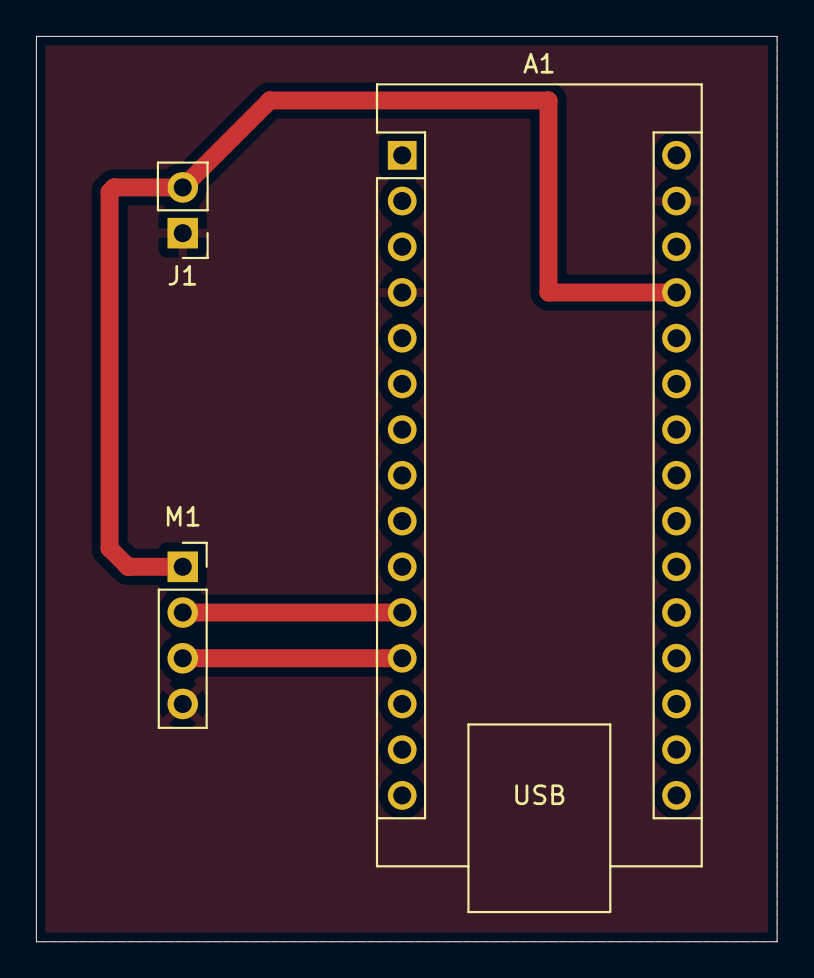
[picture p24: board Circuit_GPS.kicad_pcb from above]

Board: 2 copper layers, 41.1 x 50.3 mm, 3 parts (0 on the bottom side), 4 nets.

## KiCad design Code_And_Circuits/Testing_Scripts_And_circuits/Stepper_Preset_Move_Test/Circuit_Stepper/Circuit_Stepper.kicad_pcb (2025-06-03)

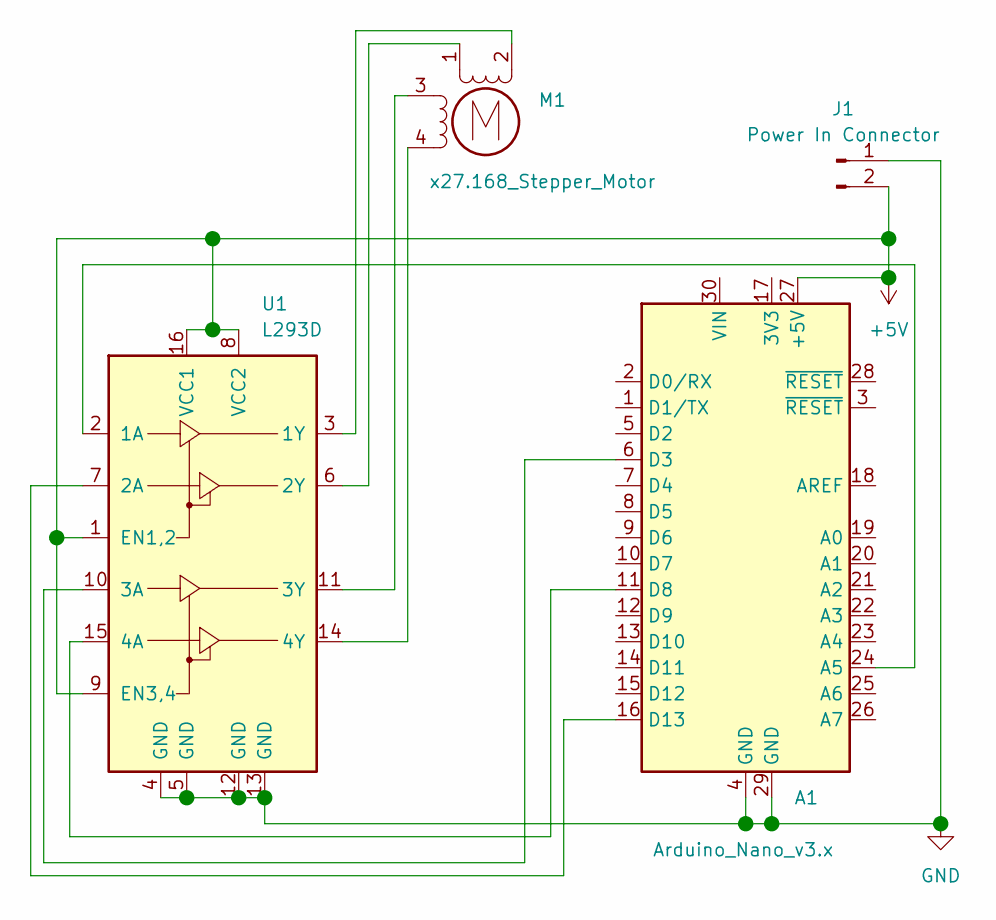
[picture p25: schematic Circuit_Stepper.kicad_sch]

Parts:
A1: Arduino_Nano_v3.x; Arduino_Nano
J1: Power In Connector; PinHeader_1x02_P2.54mm_Vertical
M1: x27.168_Stepper_Motor; X27-168
U1: L293D; DIP-16_W7.62mm

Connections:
+5V: A1.27 (+5V), J1.2, U1.1 (EN1,2), U1.8 (VCC2), U1.9 (EN3,4), U1.16 (VCC1)
GND: A1.4 (GND), A1.29 (GND), J1.1, U1.4 (GND), U1.5 (GND), U1.12 (GND), U1.13 (GND)
unnamed: A1.24 (A5), U1.2 (1A)
unnamed: A1.6 (D3), U1.10 (3A)
unnamed: A1.11 (D8), U1.15 (4A)
unnamed: A1.16 (D13), U1.7 (2A)
unnamed: M1.2 (-), U1.3 (1Y)
unnamed: M1.1, U1.6 (2Y)
unnamed: M1.3, U1.11 (3Y)
unnamed: M1.4, U1.14 (4Y)

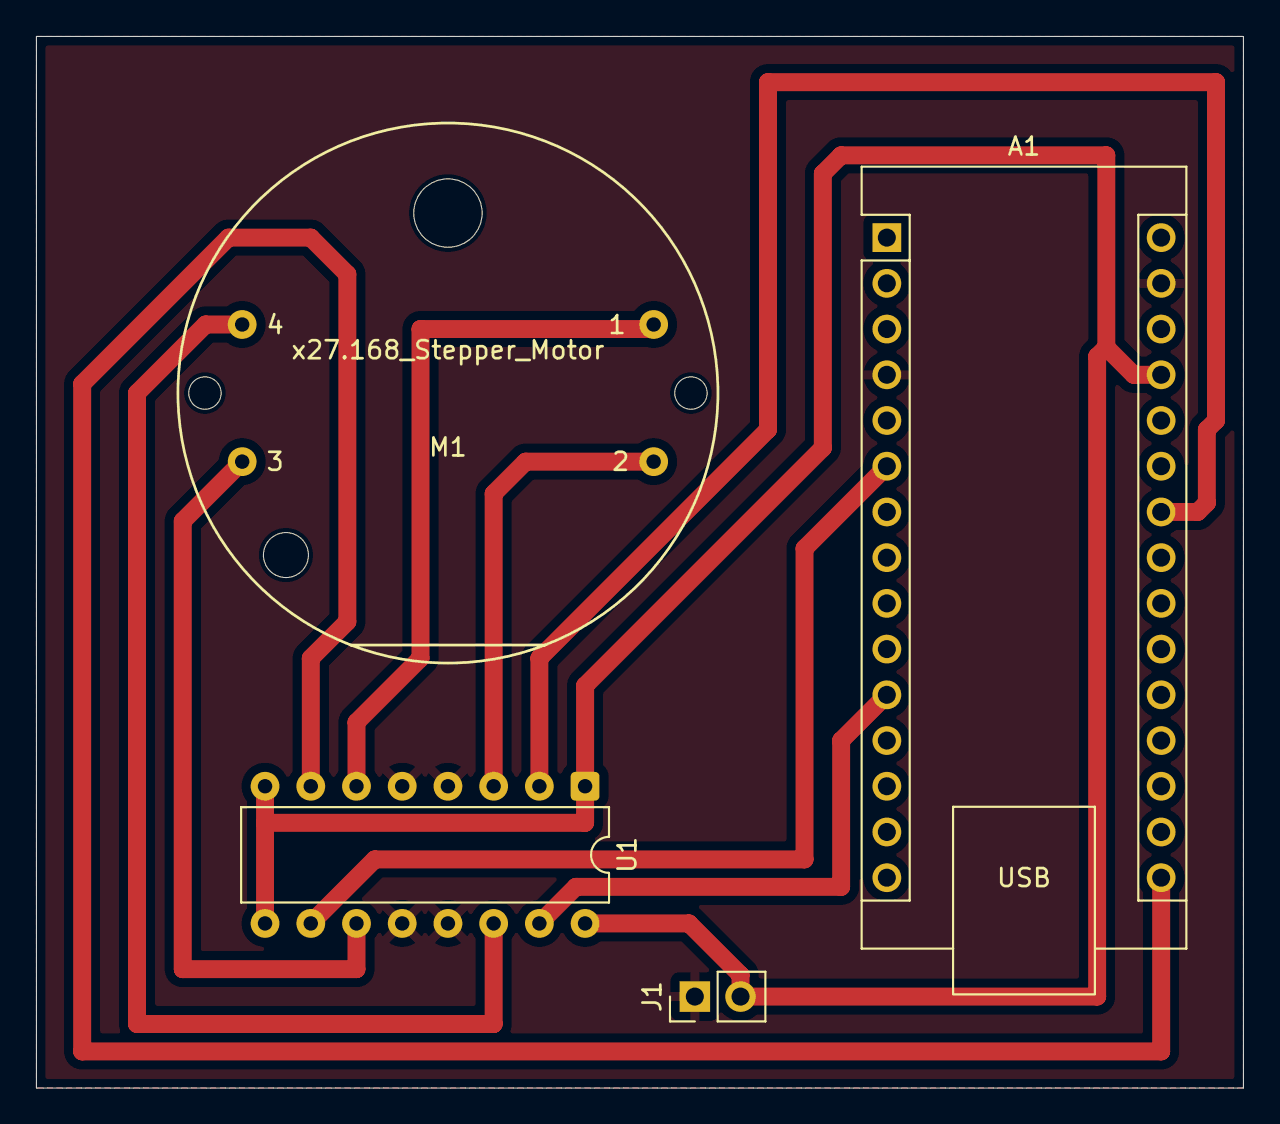
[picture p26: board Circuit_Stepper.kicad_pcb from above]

Board: 2 copper layers, 67.1 x 58.4 mm, 4 parts (0 on the bottom side), 10 nets.

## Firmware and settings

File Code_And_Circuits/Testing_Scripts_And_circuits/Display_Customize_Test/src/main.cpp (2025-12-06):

#include <Arduino.h>
#include <SPI.h> //Needed to have hardware SPI utilized.
#include <U8g2lib.h> // Library required for easy graphics management on the display.

#include "graphics.h"

//#include "private.h" // Graphics not uploaded to git repo but used in my script.

/* Creating the U8g2 constructor display class (the class call basically).
U8G2 = Start for the library.
ST7565 = The controller that is part of the display.
NHD = New haven displays.
C12832 = Defining the display it's self (the size mainly).
1,2,F drawing mode definition 1 and 2 is page based which will require a loop. F is full page buffer uses more ram than 1 and 2 but faster F is used for now.
4W_HW_SPI = 4 Wire hardware SPI mode.
Bracket Parameters:
- U8G2_R2 = defines the picture rotation, in this case 180 degree rotation, landscape as was upside down at first.
- 9 = chip select pin
- 12 = dc pin, register select pin, A0
- 10 = Reset pin
Hardware SPI was used as it will work faster than software SPI based methods in the library. Pins 13 (SPI clock pin (SPI_SCK))
and 11 (SPI data pin (COPI(MOSI))) do not need to be specified as they are the hardware SPI pins of the arduino nano esp32.
*/
U8G2_ST7565_NHD_C12832_F_4W_HW_SPI u8g2(U8G2_R2,9,12,10);


int delay_time = 5000; // Delay time between screens to make it easier to read

void setup() {
  Serial.begin(9600); //Initializing USB serial communication.
  /*
  Initializing the display
  Note due to using Pin 12 the MISO pin
  Slight initialisation changes had to be made using
  PinMode and digitalWrite
  to allow u8g2 library to work correctly with the display
  normally only the u8g2.begin() line is necessary.
  */
  pinMode(12,OUTPUT);
  digitalWrite(12,LOW);
  u8g2.begin();
  pinMode(12,OUTPUT);
  digitalWrite(12,LOW);

}

void loop() {
  // Going through each graphic type in turn to see what they all look like.
  // Basic Hello world to see initialization
  u8g2.clearBuffer();
  u8g2.setFont(u8g2_font_ncenB14_tr);
  u8g2.drawStr(0,20,"Hello World!");
  u8g2.sendBuffer();
  delay(delay_time);

  //30 segment size test Bold font for kph
  u8g2.clearBuffer();
  u8g2.drawXBM(0,0,128,32,high30seg);
  u8g2.setFont(u8g2_font_t0_30b_mr);
  u8g2.drawStr(75,20,"kph");
  u8g2.sendBuffer();
  delay(delay_time);

  //30 segment size test nonbold font for kph
  u8g2.clearBuffer();
  u8g2.drawXBM(0,0,128,32,high30seg);
  u8g2.setFont(u8g2_font_t0_30_mr);
  u8g2.drawStr(75,20,"kph");
  u8g2.sendBuffer();
  delay(delay_time);

  //32 segment size test with trip and odometer
  u8g2.clearBuffer();
  u8g2.drawXBM(0,0,128,32,high32seg);
  u8g2.setFont(u8g2_font_VCR_OSD_mr);
  u8g2.drawStr(75,18,"kph");
  u8g2.sendBuffer();
  delay(delay_time);

  // Font based speed representation
  u8g2.clearBuffer();
  u8g2.setFont(u8g2_font_inr33_mn);
  u8g2.drawStr(0,32," 42");
  u8g2.setFont(u8g2_font_t0_30_mr);
  u8g2.drawStr(80,20,"kph");
  u8g2.setFont(u8g2_font_5x7_mr);
  u8g2.drawStr(79,32,"A1000000.0");
  u8g2.sendBuffer();
  delay(delay_time);

  //RPM version a/1 test (Same)
  u8g2.clearBuffer();
  u8g2.drawXBM(0,0,128,32,rpm_a);
  u8g2.sendBuffer();
  delay(delay_time);

  //RPM version b/2 test (Ramping)
  u8g2.clearBuffer();
  u8g2.drawXBM(0,0,128,32,rpm_b);
  u8g2.sendBuffer();
  delay(delay_time);

  //Coolant and fuel version a/1 test (Ramping)
  u8g2.clearBuffer();
  u8g2.drawXBM(0,0,128,32,cool_fuel_a);
  u8g2.sendBuffer();
  delay(delay_time);

  //Coolant and fuel version b/2 test (Same)
  u8g2.clearBuffer();
  u8g2.drawXBM(0,0,128,32,cool_fuel_b);
  u8g2.sendBuffer();
  delay(delay_time); 

  /*
  * The following is used in my script but due to licencing the graphics cannot be uploaded to git
  * Commented out for git upload but used in my script. 
  

  //Private_a
  u8g2.clearBuffer();
  u8g2.drawXBM(0,0,128,32,private_a);
  u8g2.sendBuffer();
  delay(delay_time); 

  //Private_b
  u8g2.clearBuffer();
  u8g2.drawXBM(0,0,128,32,private_b);
  u8g2.sendBuffer();
  delay(delay_time);

  //Private_c
  u8g2.clearBuffer();
  u8g2.drawXBM(0,0,128,32,private_c);
  u8g2.sendBuffer();
  delay(delay_time);

  //Private_d
  u8g2.clearBuffer();
  u8g2.drawXBM(0,0,128,32,private_d);
  u8g2.sendBuffer();
  delay(delay_time);

  //Private_e
  u8g2.clearBuffer();
  u8g2.drawXBM(0,0,128,32,private_e);
  u8g2.sendBuffer();
  delay(delay_time);

  //Private_f
  u8g2.clearBuffer();
  u8g2.drawXBM(0,0,128,32,private_f);
  u8g2.sendBuffer();
  delay(delay_time);

  //Private_g
  u8g2.clearBuffer();
  u8g2.drawXBM(0,0,128,32,private_g);
  u8g2.sendBuffer();
  delay(delay_time);
  End of private section*/
}

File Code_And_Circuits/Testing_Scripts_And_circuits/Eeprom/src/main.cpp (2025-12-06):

#include <Arduino.h>

//Library imports required for I2C eeprom communication.
#include <Wire.h>
#include <SparkFun_External_EEPROM.h>

const int eeprom_chip_size = 128; // In Kibibit (kib) defined by what chip you have factors of 1024. 1 kib = 1024 bits.
int odometer_start_index = 4; // In actual script this will need to be coded in to account for all calibration settings. May help to automate to avoid errors.
// For this script Due to int in memory index 0, the first four memory addresses (bytes) will be taken (0,1,2,3) therefore we need to start writting at index 4.
int odometer_last_potential_index = ((eeprom_chip_size * 1024)/8)-4; // converted to bits then bytes, then -1 for last index and -3 for bytes required as one is already counted as last index.
// For above indexes it is assumed a int 32 value is used (4 bytes)
// Note on the esp32s int is also 4 bytes unlike the normal arduinos where int in 2 bytes. the arduino nano esp32 is 32 bit while traditional arduinos are 16bit or 8 bit.
char option_selection;
char temp[1] = {'2'}; //Just to setup the digit input for setting saving test.
int digit_to_write;
int digit_read;
// For actual settings, data type is adjusted depending on what is sutable and takes up the least amount of storage space.
// It must be noted that memory addresses will also need to be adjusted for the final design depending on the data type lengths.
int list_read;
int odometer_reading = 0; // Floats are being used to retain accurate odometer readings. anything less than 0.1 will not be displayed in final design.
int odometer_address = odometer_start_index;

ExternalEEPROM eeprom_object;

char input_digit();


void setup() {
  Serial.begin(9600);
  while (!Serial) {
    ; // wait for serial port to connect. Used for user selection code.
  }

  Wire.begin();
  eeprom_object.setMemoryType(eeprom_chip_size); // Set as 128 as that is my eeprom chip. Adjust if needed.
  if (eeprom_object.begin() == false){
    Serial.println("No memory detected code will break.");
    while (true){};
  }
  Serial.println("Memory Detected");
  Serial.print("Mem size in bytes: ");
  Serial.println(eeprom_object.length());
  eeprom_object.erase(); // Clear eeprom so that previous code execution does not mess with tests.
}


void loop() {

  // Option input section
  Serial.println("Please input option digit");
  option_selection = input_digit();

  if (option_selection == '1'){
    // Writting to the first address of the eeprom.
    Serial.println("Type digit to save");
    temp[0] = input_digit();
    digit_to_write = atoi(temp);
    eeprom_object.put(0,digit_to_write);
  }

  else if (option_selection == '2'){
    // Reading from the first eeprom address.
    eeprom_object.get(0,digit_read);
    Serial.println("The digit read is:");
    Serial.println(digit_read);
  }

  else if (option_selection == '3'){
    // Writting many odometer readings to eeprom incrementing by 1 which will represent 0.1Km
    // As each int on the esp32 arduino is 4 bytes, we must iterate 4 memory addresses over so that we do not over write portions of previous int values.
    Serial.print("Writting data to eeprom");
    // For testing reasons I am writting 1005 values where it increments by 1 for each step.
    // This helps to test writitng of data and the the resetting of memory addresses.
    for (int i=1; i<=1005;i++){
      odometer_address = odometer_address + 4;
      if (odometer_address > odometer_last_potential_index){
        // Catch to reset odometer indexes if it reaches the end of the eeprom memory
        odometer_address = odometer_start_index; 
      }
      odometer_reading ++;
      eeprom_object.put(odometer_address,odometer_reading);
    }
  }

  else if (option_selection == '4'){
    // Reading number list and outputting highest value and eeprom position
    Serial.println("Finding Highest value and address of the value");
    for (int i = odometer_start_index; i<=odometer_last_potential_index; i = i+4){
      // Reading each eeprom odometer address in turn to find the highest value
      // Returning value and address position.
      eeprom_object.get(i,list_read);
      if (odometer_reading < list_read){
        odometer_reading = list_read;
        odometer_address = i;
      }
    }
    Serial.print("Highest Odometer reading = ");
    Serial.println(odometer_reading);
    Serial.print("Highest Odometer reading address = ");
    Serial.println(odometer_address);


  }
  else{
    // Error catch.
    Serial.println("Option does not exist please type in opions 1-4");
  }
}


// Function which makes sure a digit is inputed into the serial terminal.
char input_digit(){
  char input;
  boolean is_digit = false;
  Serial.println("type digit:");
  while (is_digit == false){
    while (!Serial.available()) {};
    input = Serial.read();
    if (isdigit(input)){
      is_digit = true;
    }
    else{
      Serial.println("Not a digit please type in a digit:");
    }
  }
  return(input);
}

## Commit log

2025-05-30 Added RPM changer to RPM to PWM test script through serial interface and added a User guide for the script.
2025-06-02 Adding in more info to RPM To PWM README.md and added in circuit scematic and PCB if you wanted to use one.
    [Circuit_RPM_TO_PWM.kicad_pcb, Circuit_RPM_TO_PWM.kicad_sch]
2025-06-03 Made a circuit and started the README.md for testing the movement and circuit of the 27.168 stepper motor. Code to be done.
    [Circuit_Stepper.kicad_pcb, Circuit_Stepper.kicad_sch]
2025-06-04 Finished the stepper testing scripts, README.md and circuit diagrams.
2025-06-04 Added a write up, circuit, testing PCB and script for adding GPS to the dash project
    [Circuit_GPS.kicad_pcb, Circuit_GPS.kicad_sch]
2025-06-11 Slight coding fix to rpm to pwm math as was error and was doing int math instead of float math
    [main.cpp]
2025-06-12 Finished code and tunning of rpm counter, adding speed calculator in please note example numbers not related to anything, adjusted README.md to better reflect on pulse counter usage and thanks to ext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
    [Circuit_Pulse_Count.kicad_pcb, Circuit_Pulse_Count.kicad_sch]
2025-06-12 Have basic cycle of numbers in alphanumeric display and circuit and PCB done. Code functionization, and HOW_TO_USE.md files to be done
    [Circuit_Alphanumeric.kicad_pcb, Circuit_Alphanumeric.kicad_sch]
2025-06-13 Bar chart with shift register code compleated need circuit and HOW_TO_USE.md file made
2025-06-13 Finished write up on how to use bar chart code and made circuit schematic and pcb design
    [Cicuit_Bar.kicad_pcb, Cicuit_Bar.kicad_sch]
2025-06-14 Fixed alphanumeric HOW_TO_USE.md error and adding a testing script, schematic and HOW_TO_USE.md for a 6 axis accelerometer and gyroscope
    [Circuit_Accel_Gyro.kicad_pcb, Circuit_Accel_Gyro.kicad_sch]
2025-06-16 Started to make the KiCAD scematic and PCB/s for the project slowly planning it all out
    [Data_Display_Controller.kicad_sch, External_Conections_Conditioning.kicad_sch, Full_Circuit.kicad_pcb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]
2025-06-24 Wrote up on how the fuel level sensing circuit should be designed
    [Level_VS_Resistance_Test_calcs.ods]
2025-06-25 Wrote up on the design considerations behind the coolant monitoring circuit
    [Design_Charts.ods]
2025-06-26 Finished schematic need to do PCB design and get Tachometer reference
    [Data_Display_Controller.kicad_sch, External_Conections_Conditioning.kicad_sch, Full_Circuit.kicad_pcb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]
2025-06-26 Made a CAD model and technical drawing of the gauge face i want to use.
    [Tach_Face_Reference_CAD_Model.FCStd]
2025-06-27 Reconfired some pin assignments for cleaner layout and adding reference footprints and mostly layed out board, due to space limits logging section has been ommitted
    [Data_Display_Controller.kicad_sch, External_Conections_Conditioning.kicad_sch, Full_Circuit.kicad_pcb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]
2025-06-27 Finished PCB layout for version 1
    [Data_Display_Controller.kicad_sch, Full_Circuit.kicad_pcb]
2025-06-27 Slight modification to get more ground fill on the top layer to help with EMI
    [Full_Circuit.kicad_pcb]
2025-06-28 Slightly adjusted layout of board and made V1 gerbers. Generated PDF schematics
    [Full_Circuit-B_Cu.gbr, Full_Circuit-B_Mask.gbr, Full_Circuit-B_Paste.gbr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]
2025-07-06 Reconfigered folder organisation for multiple revisions
    [Full_Circuit-B_Cu.gbr, Full_Circuit-B_Mask.gbr, Full_Circuit-B_Paste.gbr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]
2025-07-08 Added display test and wrote notes on the V1 PCB design
